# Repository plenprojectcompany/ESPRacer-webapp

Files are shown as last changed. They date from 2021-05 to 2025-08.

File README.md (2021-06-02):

ESPRacer for WebApp | PLEN Project Company Inc.
===============================================================================

## ESPRacer for WebApp

[ESPRacer for WebApp](https://plenprojectcompany.github.io/ESPRacer-webapp/)

## Copyright (c) 2021,
- [Isaki](https://github.com/IsakiMatsubara)
- [PLEN Project Company Inc.](https://plen.jp)

## License
This software is released under [the MIT License](http://opensource.org/licenses/mit-license.php).

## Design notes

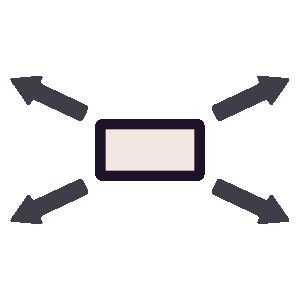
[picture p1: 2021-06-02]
image/Fullscreen-On.png

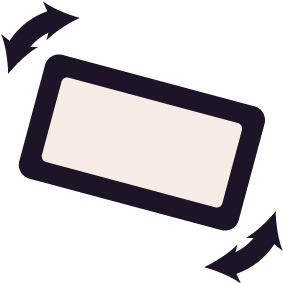
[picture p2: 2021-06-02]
image/Gyro-On.png

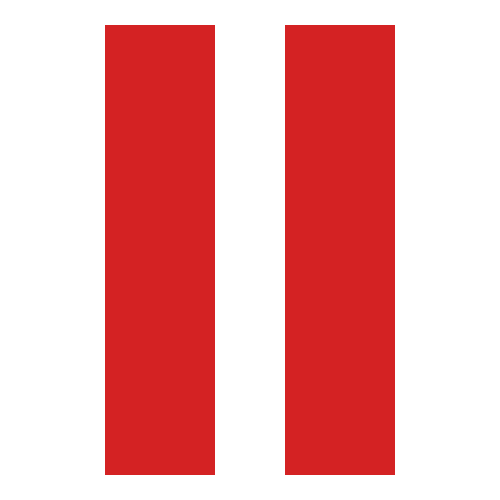
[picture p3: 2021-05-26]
image/CommandStop.png

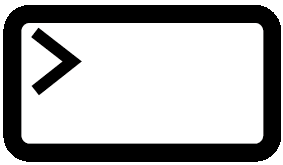
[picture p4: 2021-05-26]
image/Command.png

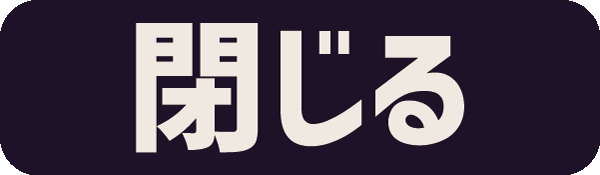
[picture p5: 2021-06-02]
image/Enter.png

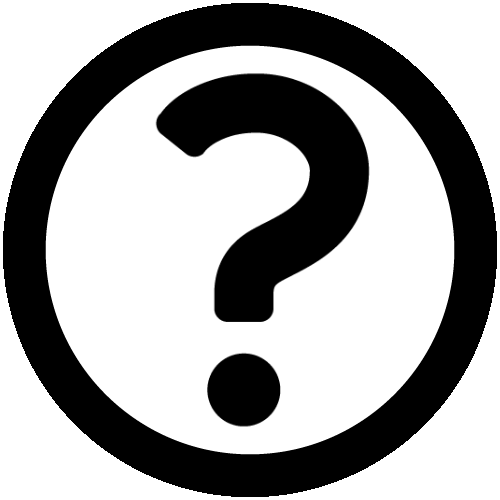
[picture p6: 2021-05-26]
image/Question.png

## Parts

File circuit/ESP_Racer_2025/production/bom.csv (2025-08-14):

Designator | Footprint | Quantity | Value | LCSC Part #
C1, C3, C4 | 0603 | 3 | 10u
C2, C5 | 0603 | 2 | 0.1u
D1 | 0603 | 1 | Status
IC1 | XCL103D503CRG | 1 | XCL102D333CR-G
J1 | Molex_PicoBlade_53047-0210_1x02_P1.25mm_Vertical | 1 | Conn_LED_1
J2 | Molex_PicoBlade_53047-0210_1x02_P1.25mm_Vertical | 1 | Conn_LED_2
J3 | Molex_PicoBlade_53047-0310_1x03_P1.25mm_Vertical | 1 | Conn_Servo
J4 | Serial | 1 | Conn_USB
Q3 | SOT23 | 1 | IRLML6402
R1, R4, R7 | 0603 | 3 | 10k
R2, R3 | 0603 | 2 | 300
R5 | 0603 | 1 | 1k
R6 | 0603 | 1 | 20k
U1 | SON50P300X200X80-13N | 1 | DRV8835DSST
U2 | FCI_SFV12R-2STE1LF | 1 | SFV12R-2STE1LF | SFV12R-2STE1LF
U3 | ESP32-C3-WROOM-02 | 1 | ESP32-C3-WROOM-02

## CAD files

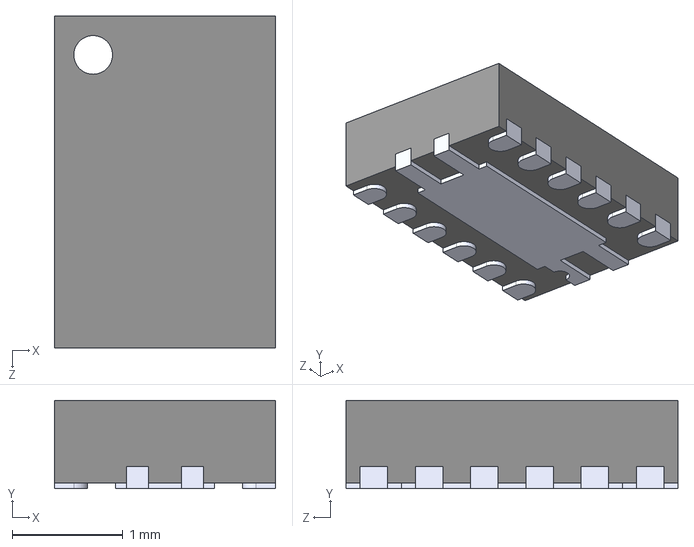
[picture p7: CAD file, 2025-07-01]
circuit/Footprint/DRV8835DSST/DRV8835DSST.step
2.00 x 0.8 x 3.00 mm

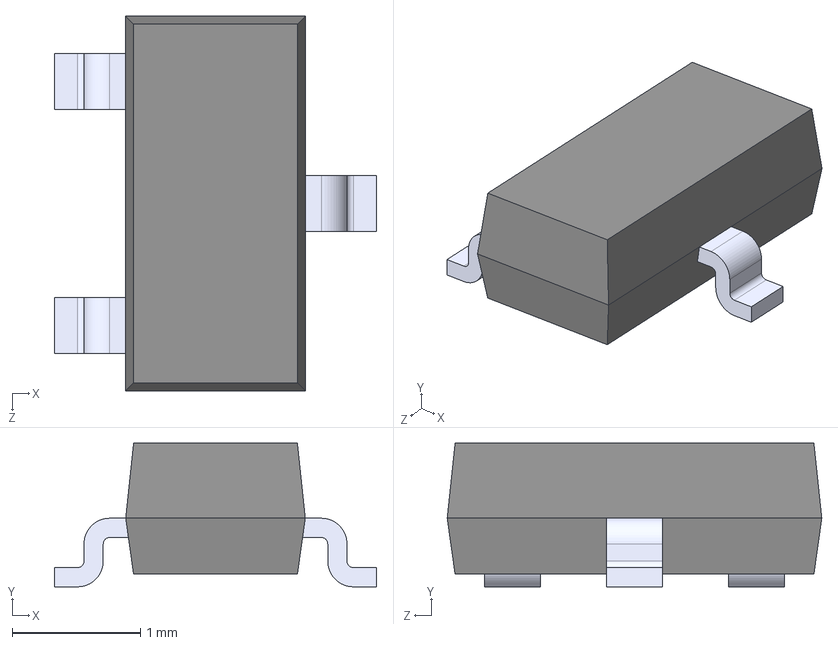
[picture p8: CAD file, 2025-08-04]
circuit/Footprint/IRLML6402/IRLML6402.step
2.51 x 1.12 x 2.92 mm

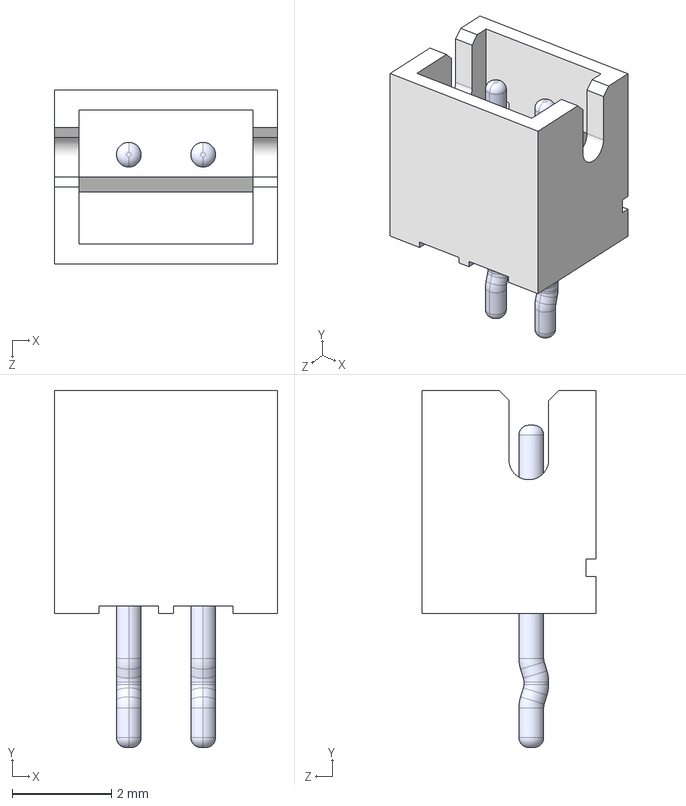
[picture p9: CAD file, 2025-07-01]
circuit/Footprint/JST_ZH_B2B-ZR_1x02_P1.50mm_Vertical/JST_ZH_B2B-ZR_1x02_P1.50mm_Vertical.STEP
4.50 x 7.20 x 3.50 mm
BxB-ZR_2
pin_Bent x 2

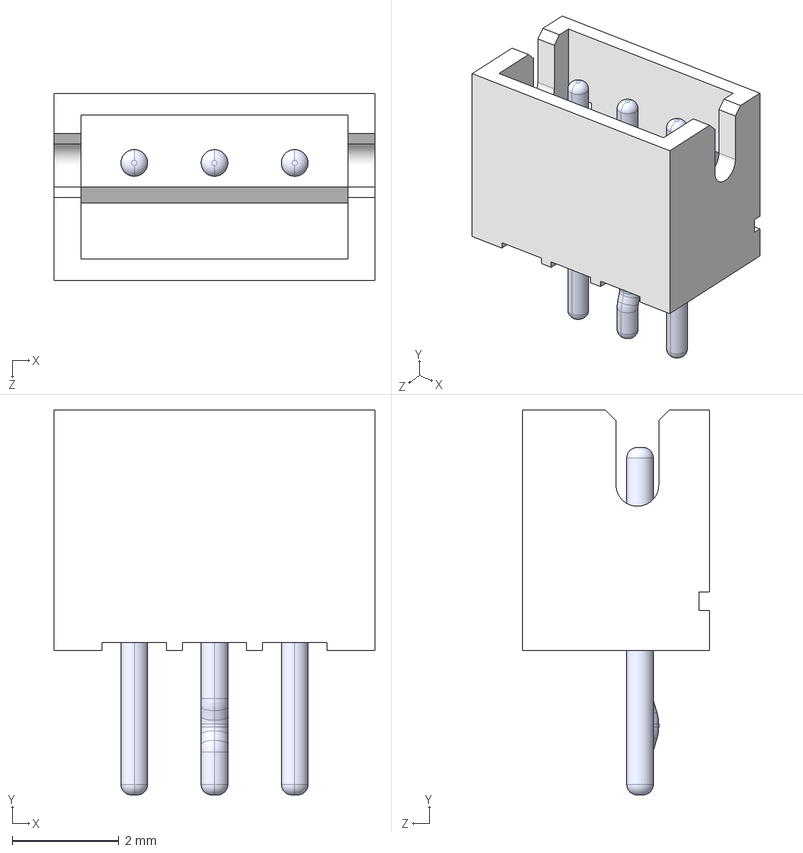
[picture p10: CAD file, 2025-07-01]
circuit/Footprint/JST_ZH_B3B-ZR_1x03_P1.50mm_Vertical/JST_ZH_B3B-ZR_1x03_P1.50mm_Vertical.STEP
6.00 x 7.20 x 3.50 mm
BxB-ZR_3
pin_straight x 2
pin_Bent

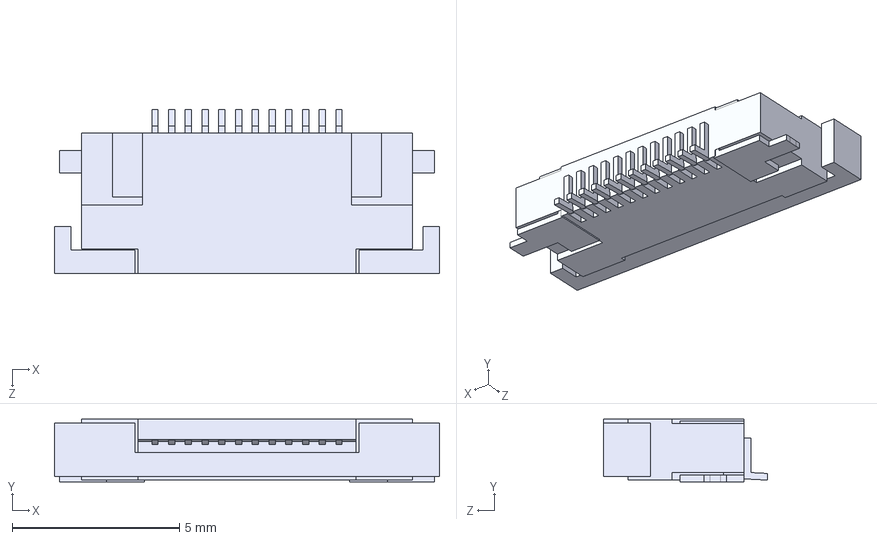
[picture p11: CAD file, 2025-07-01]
circuit/Footprint/SFV12R-2STE1LF/SFV12R-2STE1LF.step
11.5 x 1.87 x 4.90 mm

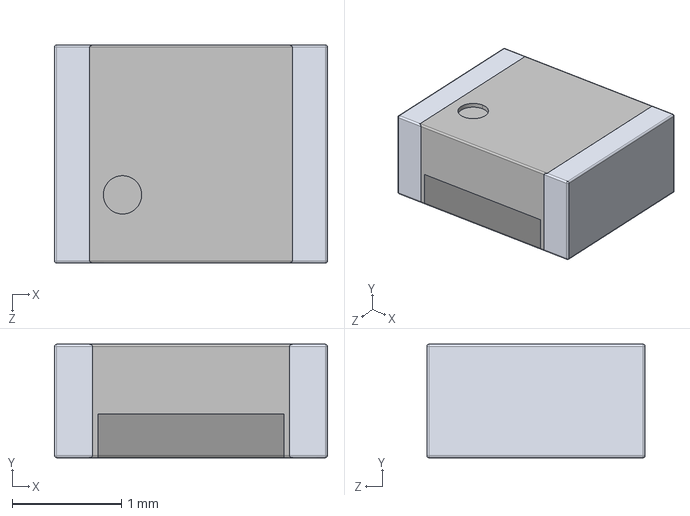
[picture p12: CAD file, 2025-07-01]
circuit/Footprint/XCL102D333CR-G/XCL102D333CR-G.stp
2.50 x 1.04 x 2.00 mm

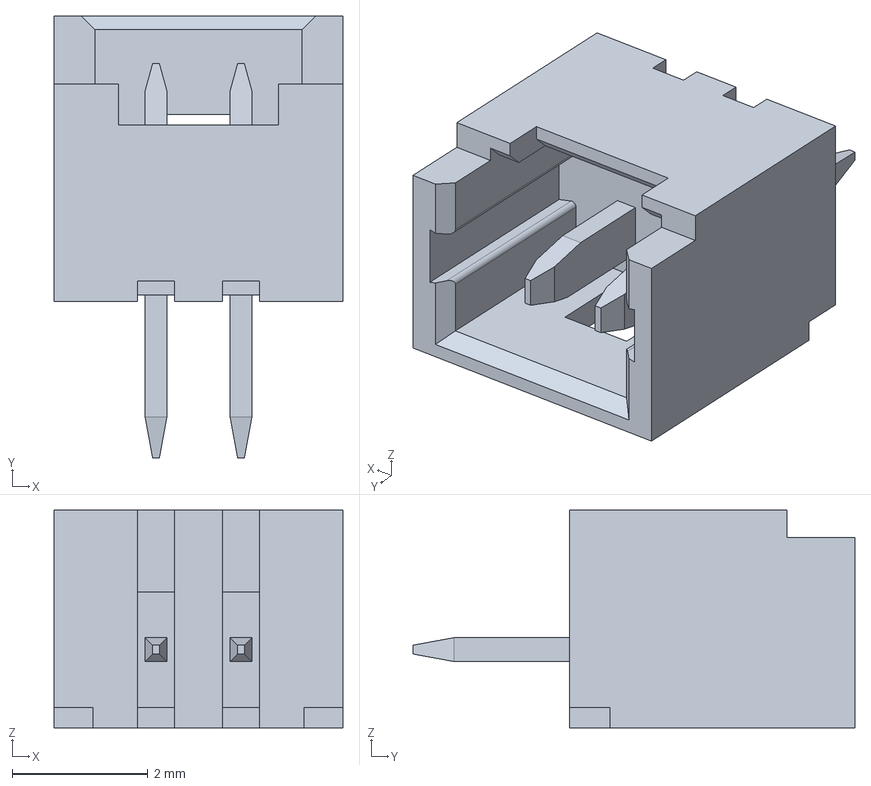
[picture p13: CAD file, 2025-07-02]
circuit/Footprint/53047-0210/53047-0210.step
4.25 x 6.50 x 3.20 mm

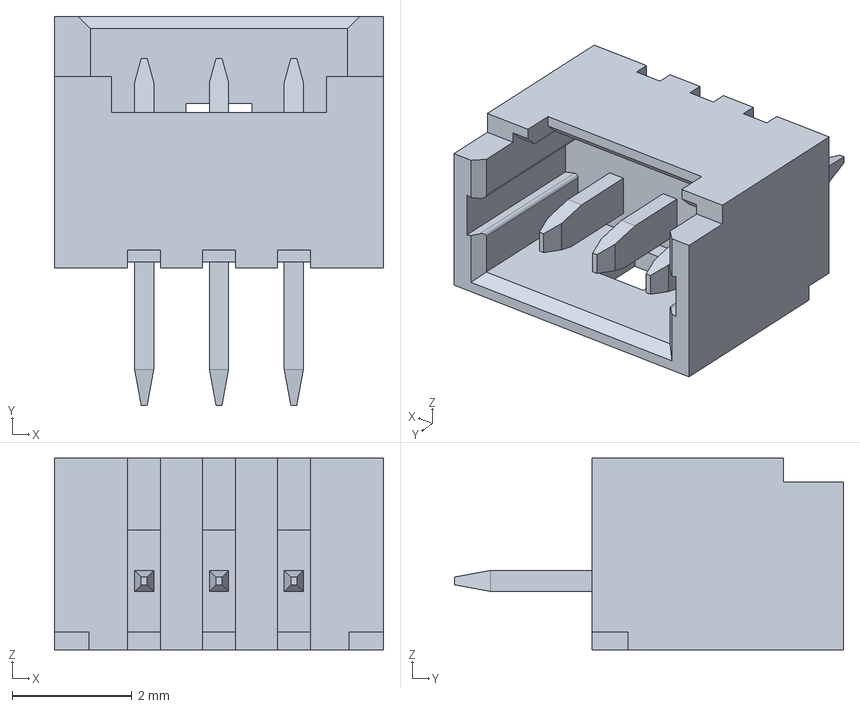
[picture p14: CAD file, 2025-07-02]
circuit/Footprint/53047-0310/53047-0310.step
5.50 x 6.50 x 3.20 mm

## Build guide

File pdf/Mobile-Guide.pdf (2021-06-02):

P.

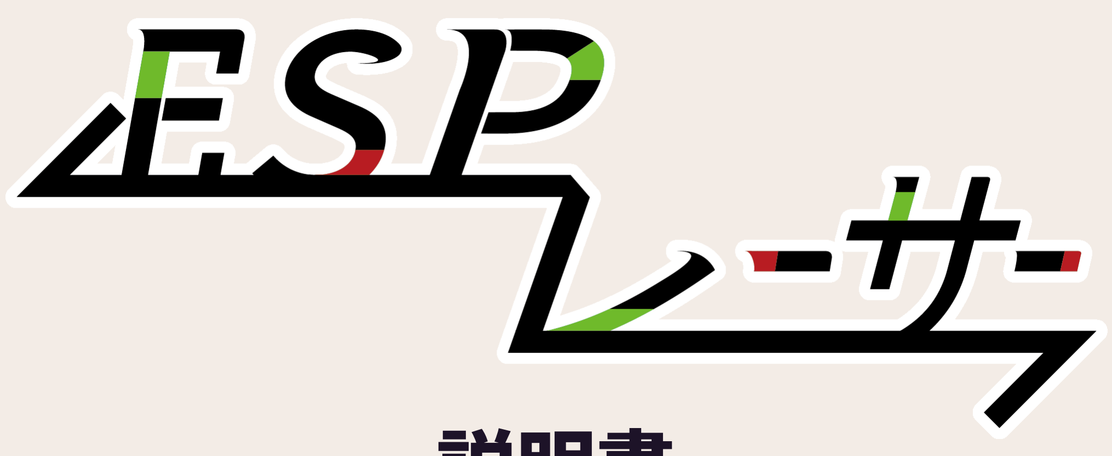
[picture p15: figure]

# 説明書

# ESPレーサー for WebApp

0

# ESPレーサーforWebApp

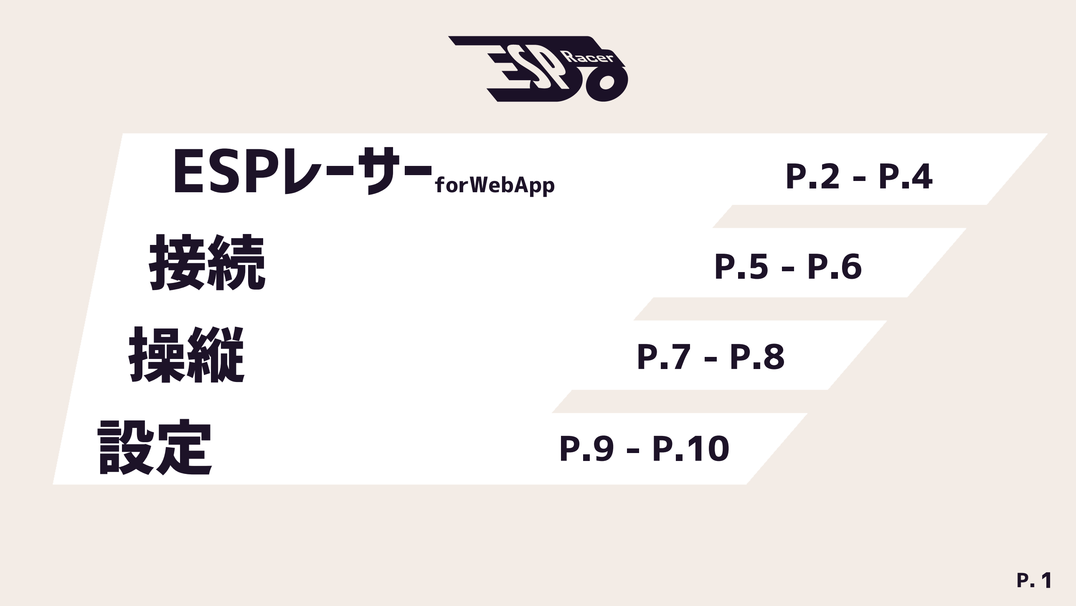
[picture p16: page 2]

P. 1

接続
操縦
設定

P.2 - P.4

P.5 - P.6

P.7 - P.8

P.9 - P.10

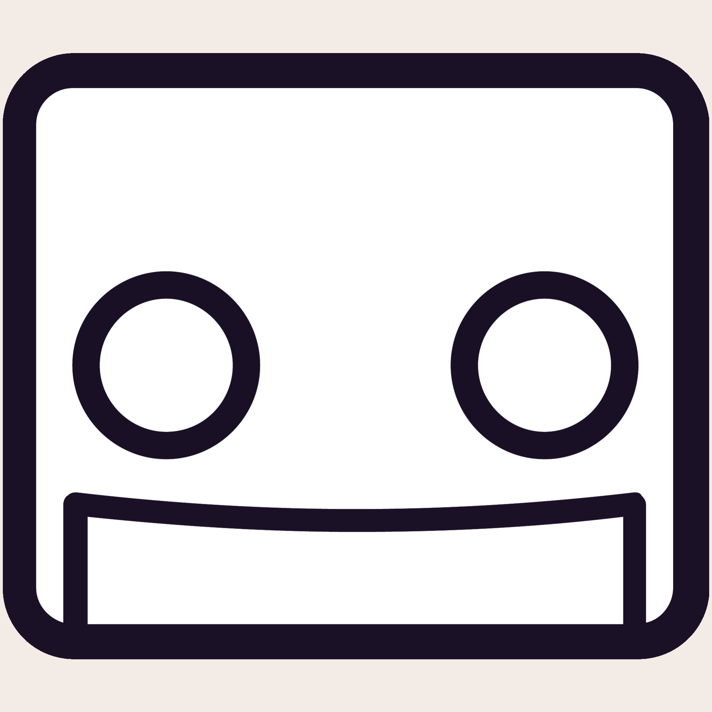
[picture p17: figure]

# ESPレーサー for WebApp

概要

2

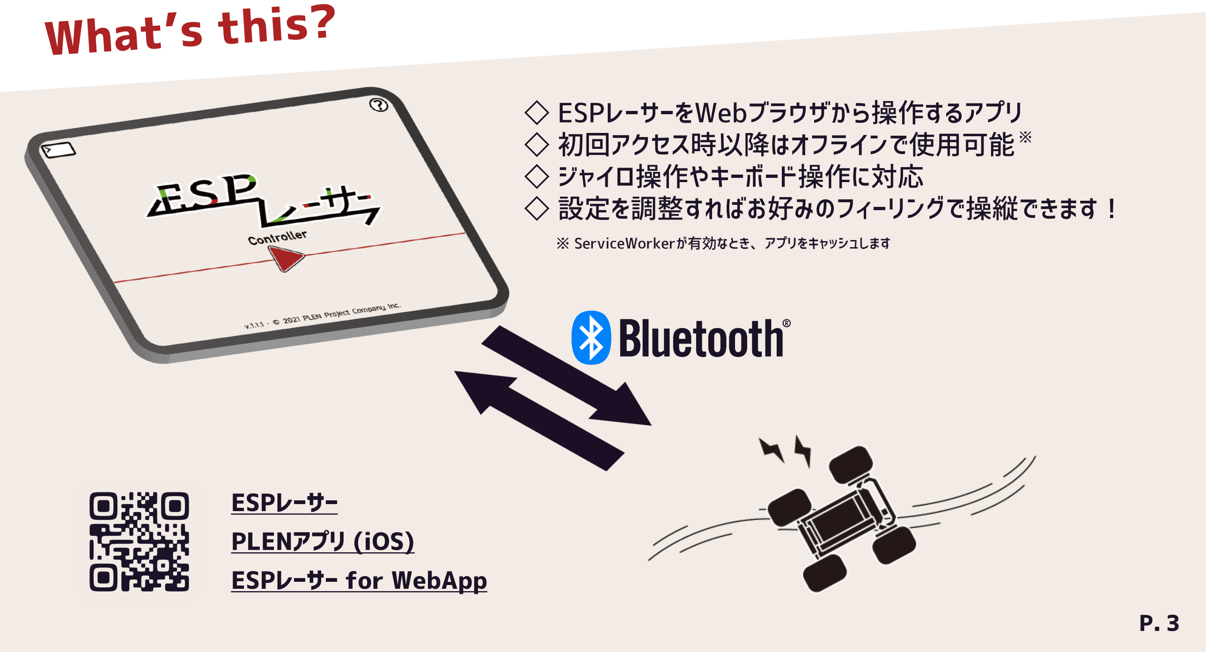
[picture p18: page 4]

P. 3

ESPレーサー for WebApp (https://plenprojectcompany.github.io/ESPRacer-webapp/index.html)

ESPレーサー (https://plen.jp/espracer/)
PLENアプリ (iOS) (https://apps.apple.com/jp/app/plen/id1561905612)

◇ ESPレーサーをWebブラウザから操作するアプリ
◇ 初回アクセス時以降はオフラインで使用可能
◇ ジャイロ操作やキーボード操作に対応
◇ 設定を調整すればお好みのフィーリングで操縦できます！

※ ServiceWorkerが有効なとき、アプリをキャッシュします

※

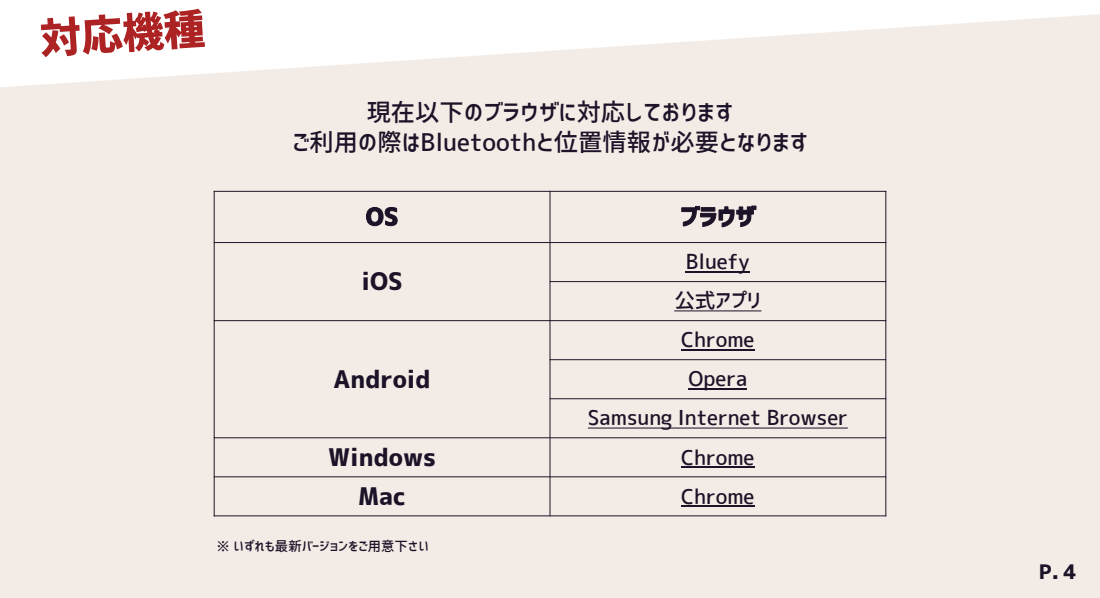
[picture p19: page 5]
公式アプリ; Android; Chrome; Opera; 現在以下のブラウザに対応しております ご利用の際はBluetoothと位置情報が必要となります; ※ いずれも最新バージョンをご用意下さい

OS | ブラウザ

iOS | Bluefy (https://apps.apple.com/us/app/bluefy-web-ble-browser/id1492822055)

Samsung Internet Browser (https://play.google.com/store/apps/details?id=com.sec.android.app.sbrowser)

Windows | Chrome (https://www.google.com/intl/ja_jp/chrome/)
Mac | Chrome (https://www.google.com/intl/ja_jp/chrome/)

接続

## 接続にはBluetoothが必要です

5

注意

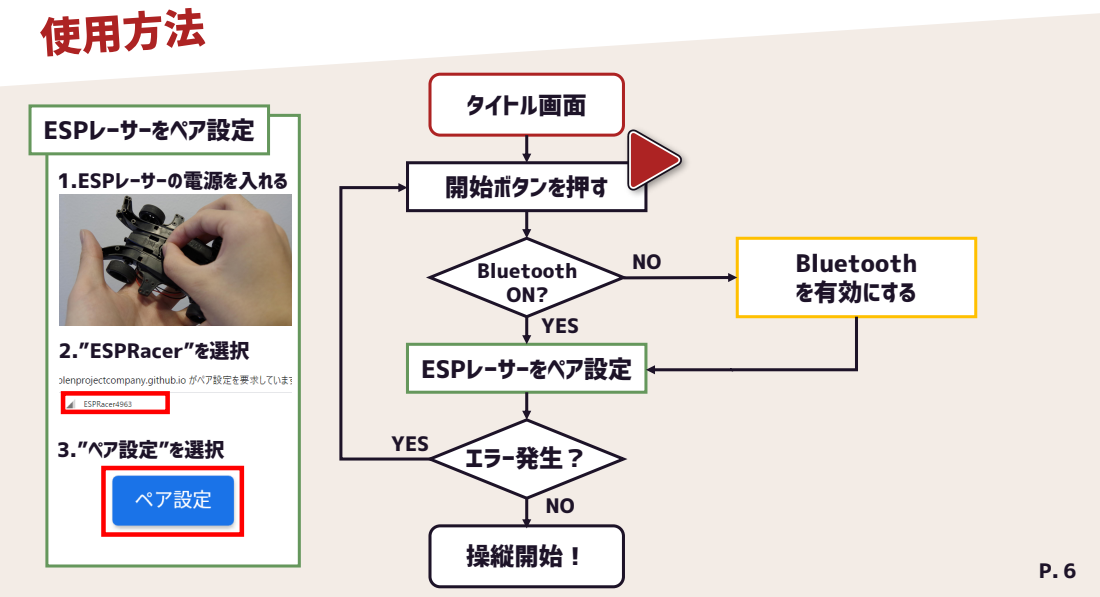
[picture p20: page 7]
タイトル画面; Bluetooth ON?; ESPレーサーをペア設定; 開始ボタンを押す; Bluetooth を有効にする; エラー発生？; 操縦開始！; YES; 1.ESPレーサーの電源を入れる; 2.”ESPRacer”を選択; 3.”ペア設定”を選択

操縦

## スマートフォンではジャイロ操作、PCではキーボード操作が可能です

7

注意

## LED

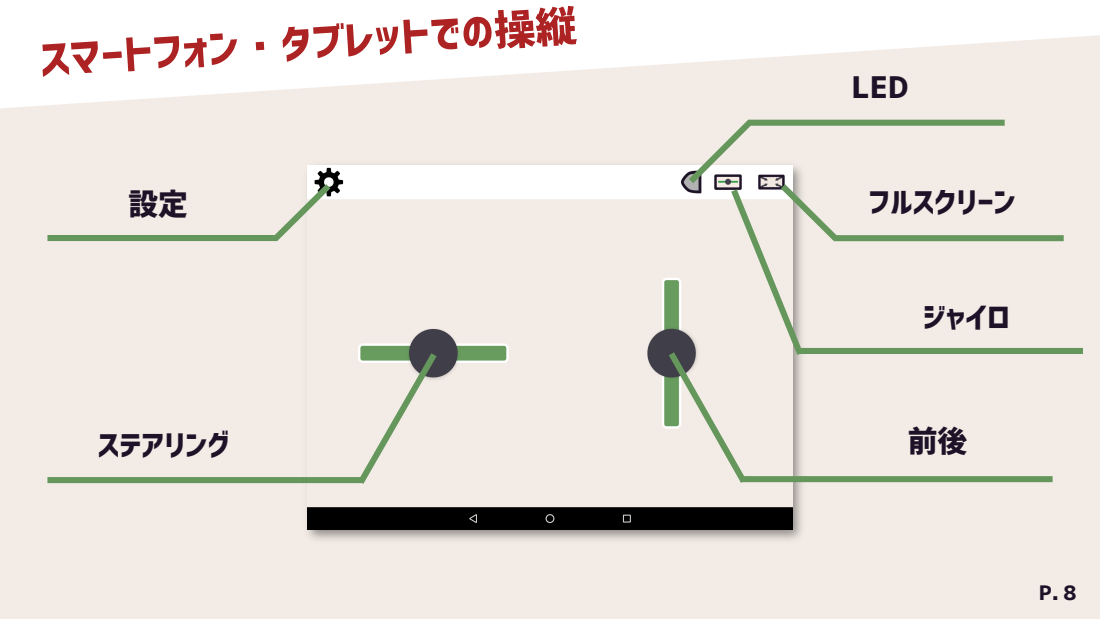
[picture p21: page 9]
ステアリング; フルスクリーン; ジャイロ

設定

## 変更した設定内容はブラウザに保存されます

9

注意

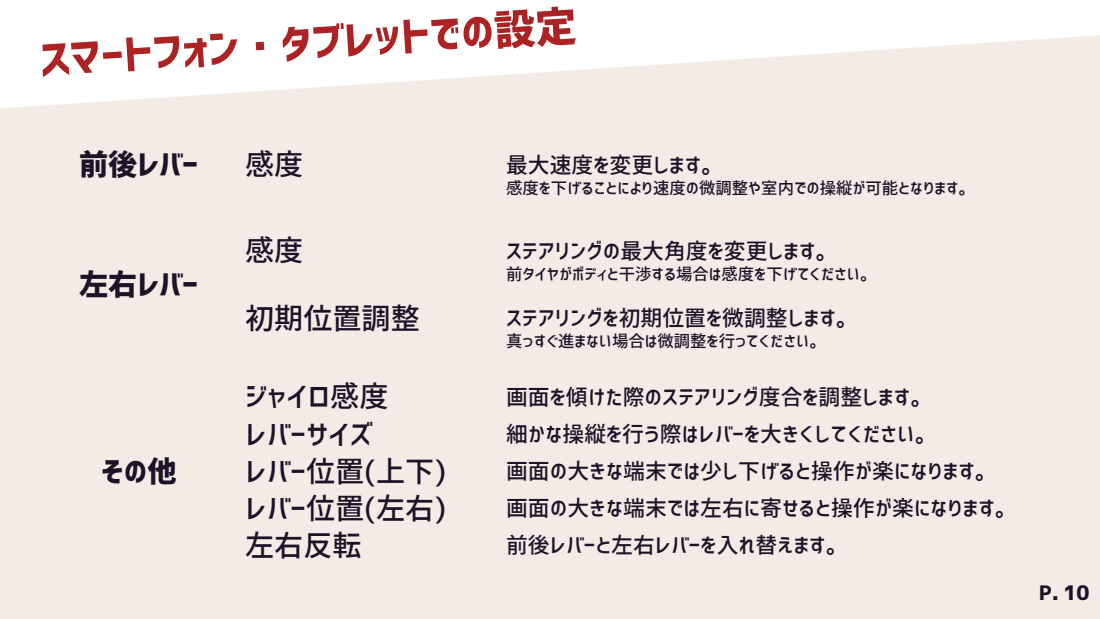
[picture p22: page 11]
前後レバー; 最大速度を変更します。; 感度を下げることにより速度の微調整や室内での操縦が可能となります。; 左右レバー; ステアリングの最大角度を変更します。; 前タイヤがボディと干渉する場合は感度を下げてください。; 初期位置調整; ステアリングを初期位置を微調整します。; 真っすぐ進まない場合は微調整を行ってください。; その他; ジャイロ感度; 画面を傾けた際のステアリング度合を調整します。; レバーサイズ; 細かな操縦を行う際はレバーを大きくしてください。; レバー位置(上下); 画面の大きな端末では少し下げると操作が楽になります。; レバー位置(左右); 画面の大きな端末では左右に寄せると操作が楽になります。; 左右反転; 前後レバーと左右レバーを入れ替えます。

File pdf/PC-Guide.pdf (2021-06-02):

P.


# 説明書

# ESPレーサー for WebApp

0

# ESPレーサーforWebApp

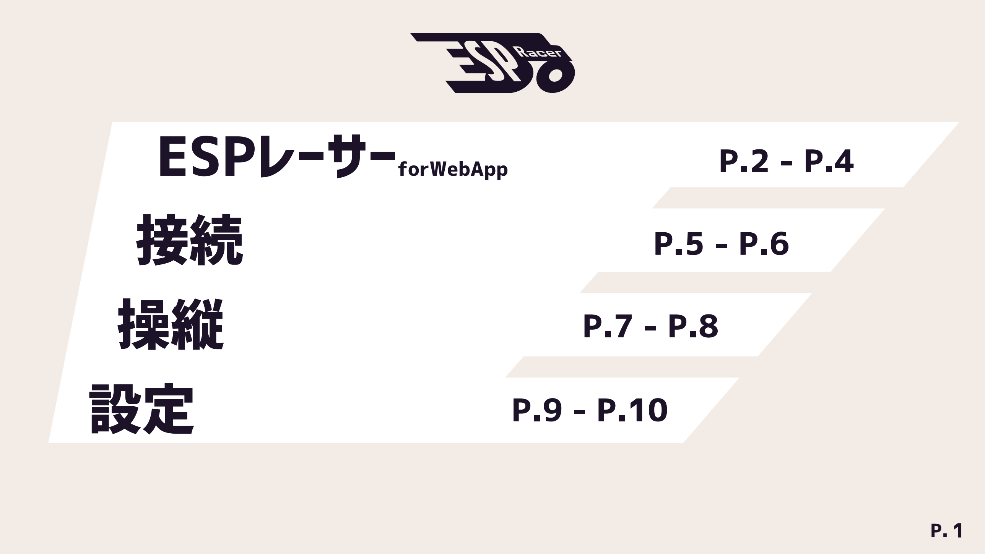
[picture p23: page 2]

P. 1

接続
操縦
設定

P.2 - P.4

P.5 - P.6

P.7 - P.8

P.9 - P.10


# ESPレーサー for WebApp

概要

2


P. 3

ESPレーサー for WebApp (https://plenprojectcompany.github.io/ESPRacer-webapp/index.html)

ESPレーサー (https://plen.jp/espracer/)
PLENアプリ (iOS) (https://apps.apple.com/jp/app/plen/id1561905612)

◇ ESPレーサーをWebブラウザから操作するアプリ
◇ 初回アクセス時以降はオフラインで使用可能
◇ ジャイロ操作やキーボード操作に対応
◇ 設定を調整すればお好みのフィーリングで操縦できます！

※ ServiceWorkerが有効なとき、アプリをキャッシュします

※

公式アプリ; Android; Chrome; Opera; 現在以下のブラウザに対応しております ご利用の際はBluetoothと位置情報が必要となります; ※ いずれも最新バージョンをご用意下さい

OS | ブラウザ

iOS | Bluefy (https://apps.apple.com/us/app/bluefy-web-ble-browser/id1492822055)

Samsung Internet Browser (https://play.google.com/store/apps/details?id=com.sec.android.app.sbrowser)

Windows | Chrome (https://www.google.com/intl/ja_jp/chrome/)
Mac | Chrome (https://www.google.com/intl/ja_jp/chrome/)

接続

## 接続にはBluetoothが必要です

5

注意

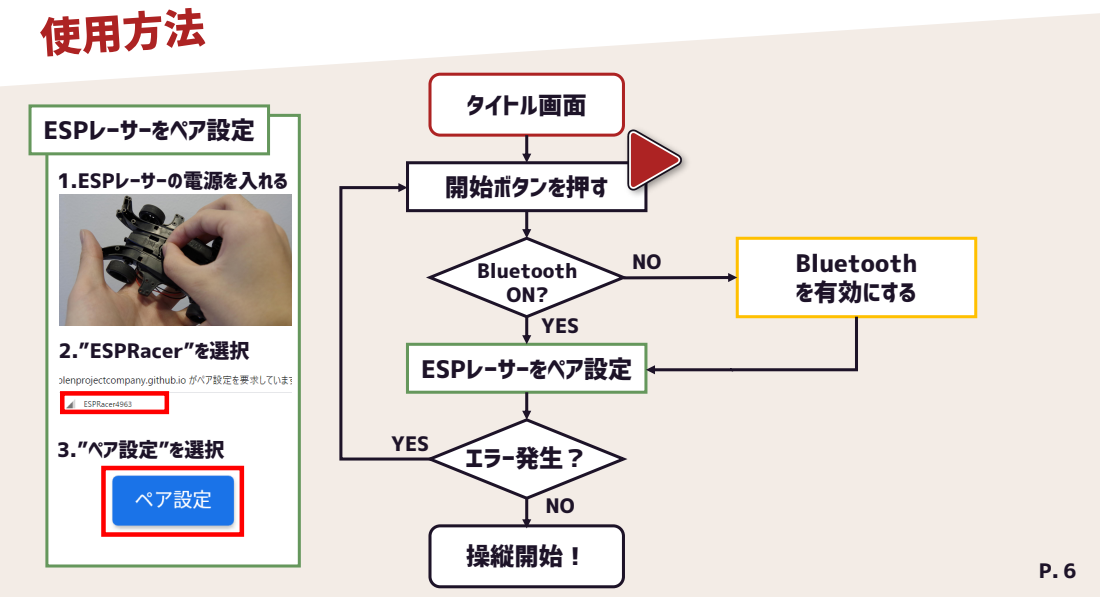
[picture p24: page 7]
タイトル画面; Bluetooth ON?; ESPレーサーをペア設定; 開始ボタンを押す; Bluetooth を有効にする; エラー発生？; 操縦開始！; YES; 1.ESPレーサーの電源を入れる; 2.”ESPRacer”を選択; 3.”ペア設定”を選択

操縦

## スマートフォンではジャイロ操作、PCではキーボード操作が可能です

7

注意

## LED

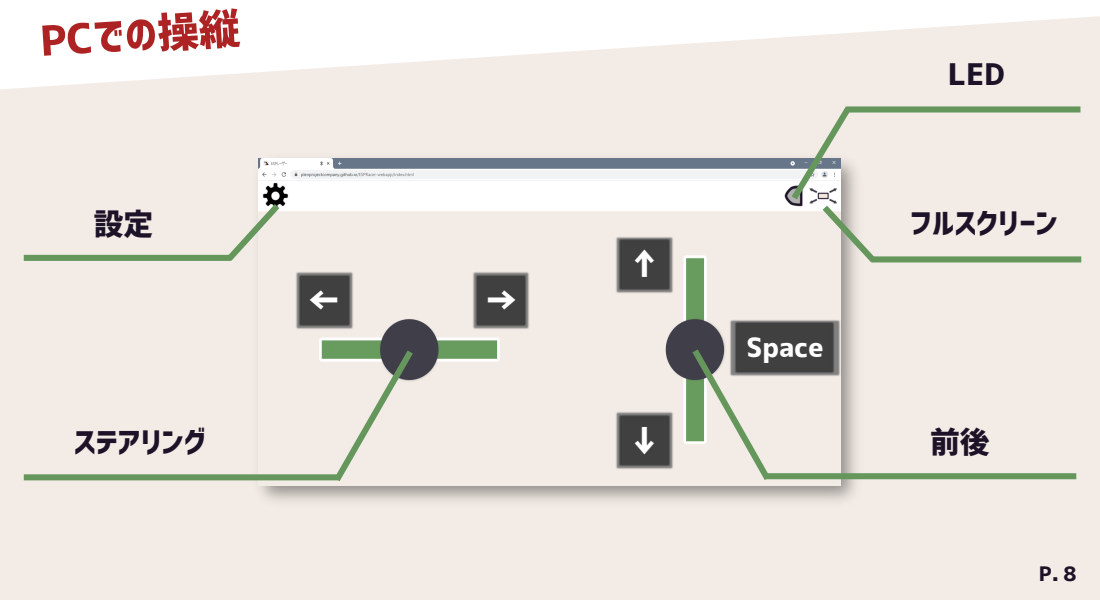
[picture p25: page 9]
ステアリング; フルスクリーン; Space

設定

## 変更した設定内容はブラウザに保存されます

9

注意

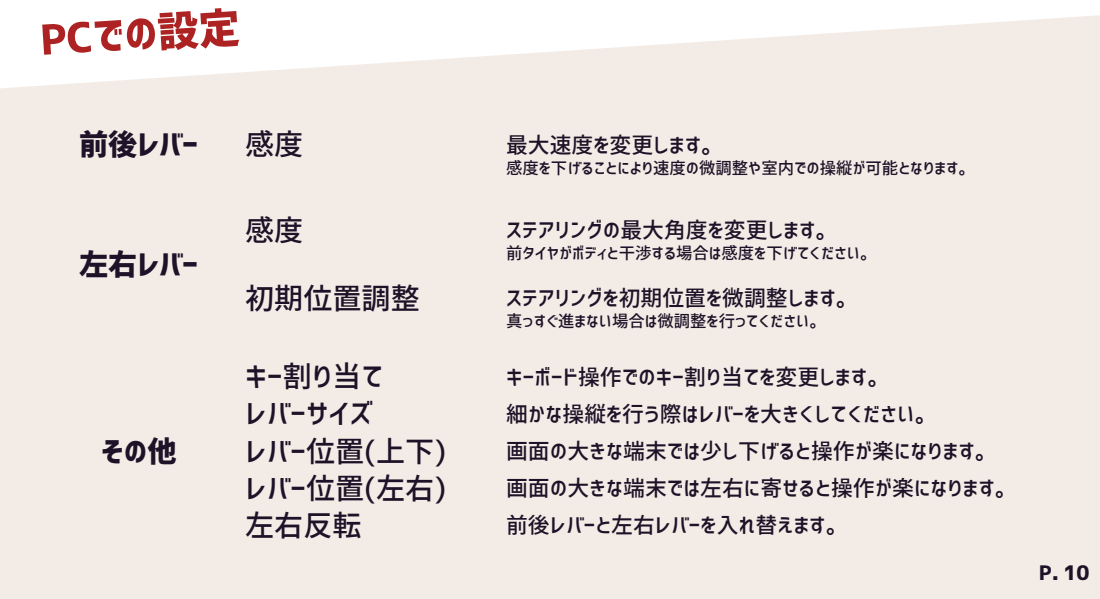
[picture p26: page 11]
前後レバー; 最大速度を変更します。; 感度を下げることにより速度の微調整や室内での操縦が可能となります。; 左右レバー; ステアリングの最大角度を変更します。; 前タイヤがボディと干渉する場合は感度を下げてください。; 初期位置調整; ステアリングを初期位置を微調整します。; 真っすぐ進まない場合は微調整を行ってください。; その他; キー割り当て; キーボード操作でのキー割り当てを変更します。; レバーサイズ; 細かな操縦を行う際はレバーを大きくしてください。; レバー位置(上下); 画面の大きな端末では少し下げると操作が楽になります。; レバー位置(左右); 画面の大きな端末では左右に寄せると操作が楽になります。; 左右反転; 前後レバーと左右レバーを入れ替えます。

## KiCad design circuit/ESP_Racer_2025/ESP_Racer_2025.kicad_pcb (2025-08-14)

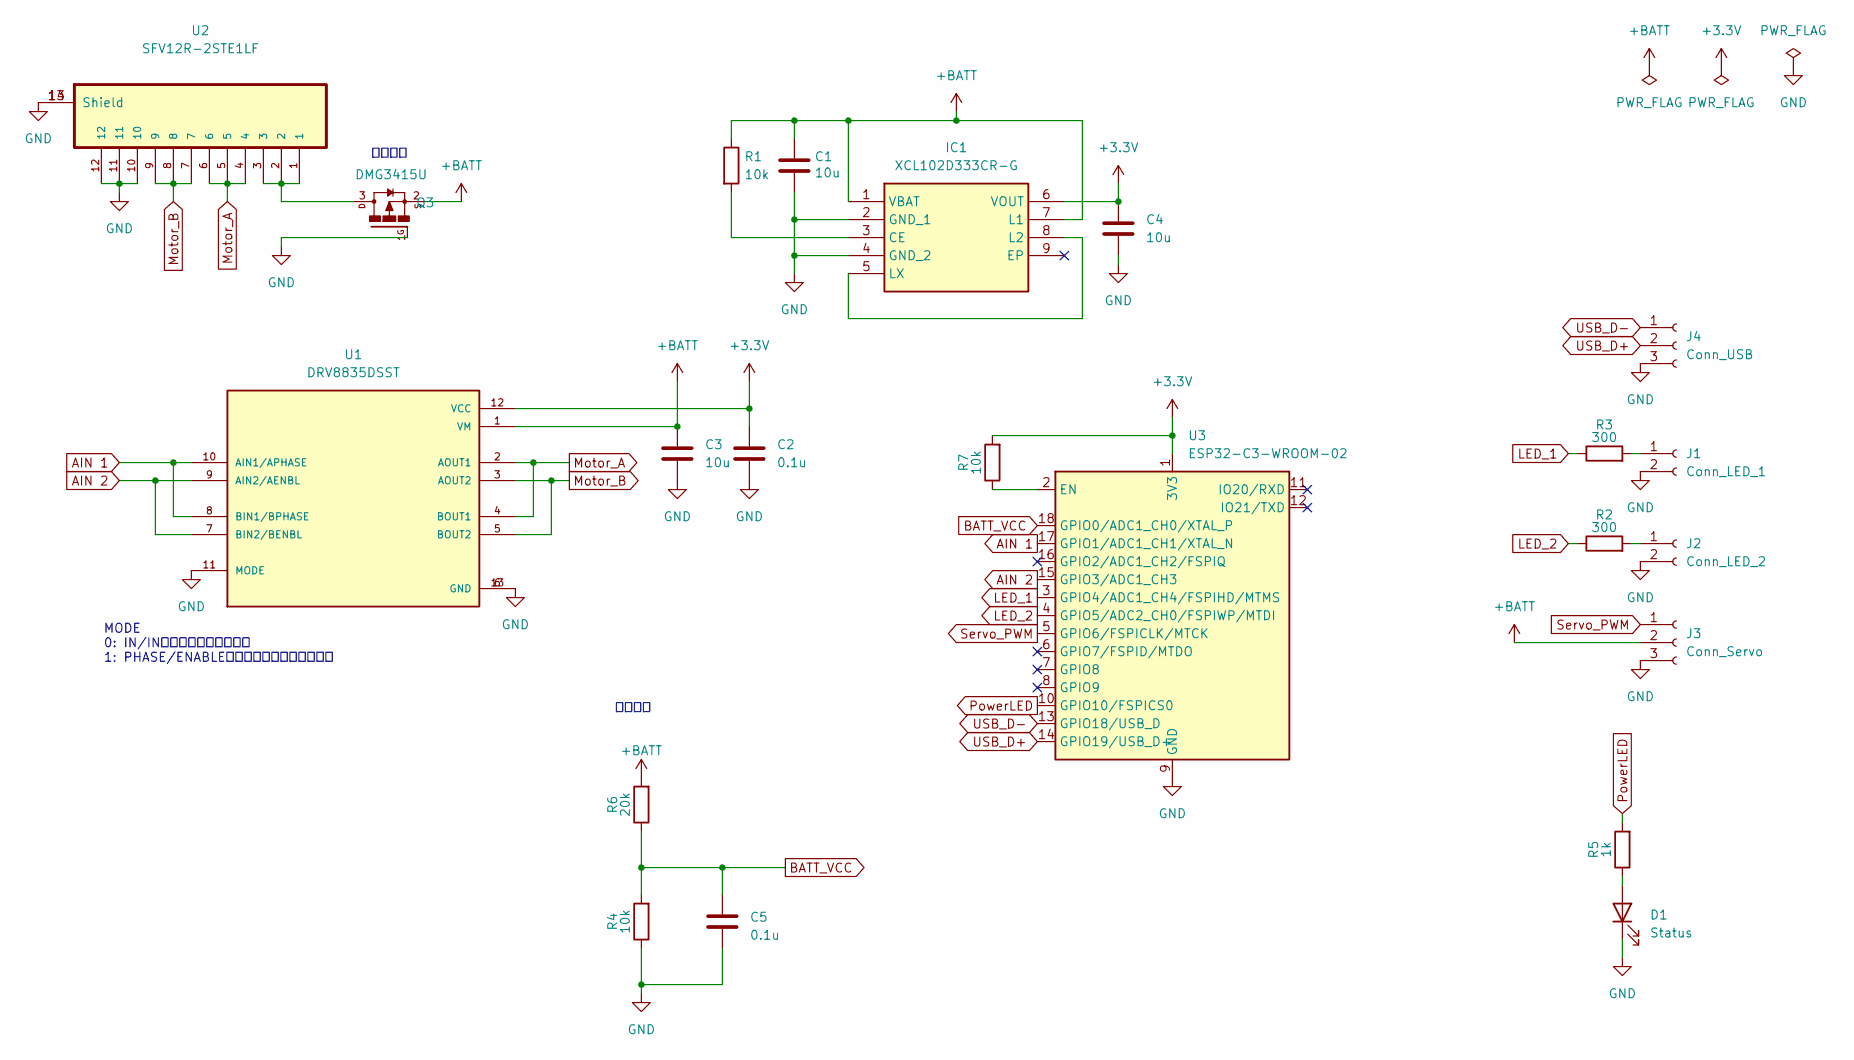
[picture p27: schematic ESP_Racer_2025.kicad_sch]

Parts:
C1, C3, C4: 10u; C_0603_1608Metric_Pad1.08x0.95mm_HandSolder
C2, C5: 0.1u; C_0603_1608Metric_Pad1.08x0.95mm_HandSolder
D1: Status; LED_0603_1608Metric_Pad1.05x0.95mm_HandSolder
IC1: XCL102D333CR-G; XCL103D503CRG; Manufacturer_Part_Number XCL102D333CR-G
J1: Conn_LED_1; Molex_PicoBlade_53047-0210_1x02_P1.25mm_Vertical
J2: Conn_LED_2; Molex_PicoBlade_53047-0210_1x02_P1.25mm_Vertical
J3: Conn_Servo; Molex_PicoBlade_53047-0310_1x03_P1.25mm_Vertical
J4: Conn_USB; Serial
Q3: DMG3415U; SOT23
R1, R4, R7: 10k; R_0603_1608Metric_Pad0.98x0.95mm_HandSolder
R2, R3: 300; R_0603_1608Metric_Pad0.98x0.95mm_HandSolder
R5: 1k; R_0603_1608Metric_Pad0.98x0.95mm_HandSolder
R6: 20k; R_0603_1608Metric_Pad0.98x0.95mm_HandSolder
U1: DRV8835DSST; SON50P300X200X80-13N; PARTREV H
U2: SFV12R-2STE1LF; FCI_SFV12R-2STE1LF; MPN SFV12R-2STE1LF
U3: ESP32-C3-WROOM-02

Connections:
+3.3V: C2.1, C4.1, IC1.6 (VOUT), R7.2, U1.12 (VCC), U3.1 (3V3)
+BATT: C1.1, C3.1, IC1.1 (VBAT), IC1.7 (L1), J3.2, Q3.2, R1.1, R6.2, U1.1 (VM)
AIN 1: U1.8 (BIN1/BPHASE), U1.10 (AIN1/APHASE), U3.17 (GPIO1/ADC1_CH1/XTAL_N)
AIN 2: U1.7 (BIN2/BENBL), U1.9 (AIN2/AENBL), U3.15 (GPIO3/ADC1_CH3)
BATT_VCC: C5.1, R4.2, R6.1, U3.18 (GPIO0/ADC1_CH0/XTAL_P)
GND: C1.2, C2.2, C3.2, C4.2, C5.2, D1.1 (K), IC1.2 (GND_1), IC1.4 (GND_2), J1.2, J2.2, J3.3, J4.3, Q3.1, R4.1, U1.6 (GND), U1.11 (MODE), U1.13 (GND), U2.10, U2.11, U2.12, U2.13 (Shield), U2.14 (Shield), U3.9 (GND), U3.19 (GND)
LED_1: R3.1, U3.3 (GPIO4/ADC1_CH4/FSPIHD/MTMS)
LED_2: R2.1, U3.4 (GPIO5/ADC2_CH0/FSPIWP/MTDI)
Motor_A: U1.2 (AOUT1), U1.4 (BOUT1), U2.4, U2.5, U2.6
Motor_B: U1.3 (AOUT2), U1.5 (BOUT2), U2.7, U2.8, U2.9
unnamed: D1.2 (A), R5.1
unnamed: IC1.3 (CE), R1.2
unnamed: IC1.5 (LX), IC1.8 (L2)
unnamed: J1.1, R3.2
unnamed: J2.1, R2.2
unnamed: Q3.3, U2.1, U2.2, U2.3
unnamed: R7.1, U3.2 (EN)
PowerLED: R5.2, U3.10 (GPIO10/FSPICS0)
Servo_PWM: J3.1, U3.5 (GPIO6/FSPICLK/MTCK)
USB_D+: J4.2, U3.14 (GPIO19/USB_D+)
USB_D-: J4.1, U3.13 (GPIO18/USB_D)

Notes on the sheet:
MODE 0: IN/INモード（慣性で停止） 1: PHASE/ENABLEモード（ブレーキで停止）
電圧監視
逆接防止

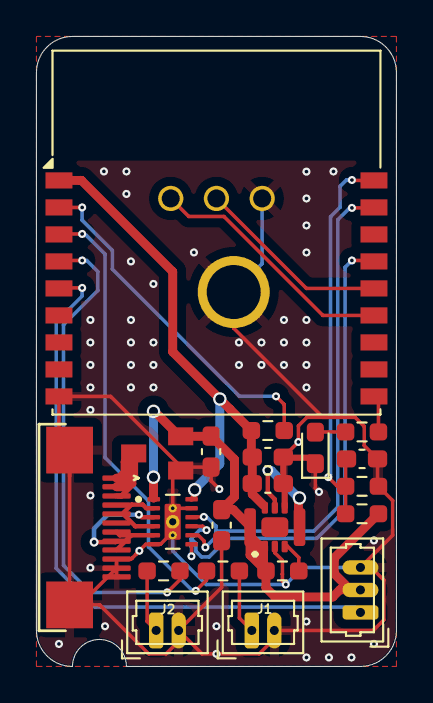
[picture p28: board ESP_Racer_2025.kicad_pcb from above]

Board: 2 copper layers, 20.0 x 35.0 mm, 22 parts (1 on the bottom side), 21 nets.

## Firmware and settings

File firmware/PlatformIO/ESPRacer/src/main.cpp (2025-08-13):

#include <Arduino.h>
#include <math.h>
#include <Wire.h>

#include <Preferences.h>

// Bluetooth Low Energy
#include "BLE/BLE.h"

#define ARRAY_LENGTH(array) (sizeof(array) / sizeof(array[0]))

#define debugMode true

/*========== Version ==========*/
#define FIRMWARE_VER "F1.02"
#define HARDWARE_VER "H1.01"

/*========== Class ==========*/
Preferences pref;

/*========== Hardware Functions ==========*/
#define MOTOR_CH 0b10 // モーターCh1
#define SERVO_CH 0b0001 // サーボ Ch0
#define PORT_CH 0b0011 // LEDポート Ch0, Ch1

/*========== I/O (ESP32-C3) ==========*/
#define STATUS_LED_PIN  10
#define SERVO_PIN  6
#define MOTOR_A_PIN 1
#define MOTOR_B_PIN 3
#define PORT_0_PIN  4
#define PORT_1_PIN  5 
#define BATT_VOL_PIN  0

#define CHANNEL_STATUS_LED_PIN 0
#define CHANNEL_SERVO_PIN 1
#define CHANNEL_MOTOR_A_PIN 2
#define CHANNEL_MOTOR_B_PIN 3

#define SERVO_FREQUENCY 50 // 50 [Hz] = 20 [ms] / 1周期
#define SERVO_RESOLUTION 12 // 12bit=4096
#define SERVO_TIME_MIN 102 // 0.5 [ms] / 20 [ms] * 4096 = 102.4
#define SERVO_TIME_MAX 492 // 2.4 [ms] / 20 [ms] * 4096 = 491.52  491.52-102.4=389.12 > 256 (OK)

/*========== BLE UUID ==========*/
#define ADVERTISING_UUID    "389CAAF0-843F-4D3B-959D-C954CCE14655"
#define SERVICE_UUID        "389CAAF0-843F-4D3B-959D-C954CCE14655"
#define GET_BATTERY_VOLTAGE "389CAAF1-843F-4D3B-959D-C954CCE14655"
#define SET_MOTOR_PWM       "389CAAF2-843F-4D3B-959D-C954CCE14655"
#define SET_PORT_OUT        "389CAAF3-843F-4D3B-959D-C954CCE14655"
#define SET_SERVO_POSITION  "389CAAF4-843F-4D3B-959D-C954CCE14655"
#define BURST_COMMAND       "389CAAF5-843F-4D3B-959D-C954CCE14655"
#define GET_FUNCTIONS       "389CAAFF-843F-4D3B-959D-C954CCE14655"

/*========== BLE CharaCharacteristic ==========*/
BLECharacteristic *GET_BATTERY_VOLTAGE_CHARA;
BLECharacteristic *SET_MOTOR_PWM_CHARA;
BLECharacteristic *SET_PORT_OUT_CHARA;
BLECharacteristic *SET_SERVO_POSITION_CHARA;
BLECharacteristic *BURST_COMMAND_CHARA;
BLECharacteristic *GET_FUNCTIONS_CHARA;

BLE RacerBLE = BLE("ESPRacer", true);

/*========== Parameters ==========*/
const int deviceIdLen = 10;
const int sendFreqency = 50; // [ms]
const bool motorInv = false;
const bool servoInv = false;

/*========== Private Variable ==========*/
bool deviceConnectedFlag = false;
int lastSendTime = 0;
int ledBlinkTime = 0;
// unsigned char motor_power = 127;
// unsigned char servo_power = 127;
// bool port0_led = false;
// bool port1_led = false;

void HardwareReset();

void SetupRacer()
{
  pinMode(STATUS_LED_PIN, OUTPUT);
  pinMode(SERVO_PIN,OUTPUT);
  pinMode(MOTOR_A_PIN, OUTPUT);
  pinMode(MOTOR_B_PIN, OUTPUT);
  pinMode(PORT_0_PIN, OUTPUT);
  pinMode(PORT_1_PIN, OUTPUT);
  pinMode(BATT_VOL_PIN, INPUT);

  // pwmの設定 channel,周波数,解像度
  ledcSetup(CHANNEL_STATUS_LED_PIN, 1000, 8);
  ledcSetup(CHANNEL_SERVO_PIN, SERVO_FREQUENCY, SERVO_RESOLUTION);
  ledcSetup(CHANNEL_MOTOR_A_PIN, 1000, 7);
  ledcSetup(CHANNEL_MOTOR_B_PIN, 1000, 7);
  // ピンをチャンネルに接続
  ledcAttachPin(STATUS_LED_PIN, CHANNEL_STATUS_LED_PIN);
  ledcAttachPin(SERVO_PIN, CHANNEL_SERVO_PIN);
  ledcAttachPin(MOTOR_A_PIN, CHANNEL_MOTOR_A_PIN);
  ledcAttachPin(MOTOR_B_PIN, CHANNEL_MOTOR_B_PIN);

  ledcWrite(CHANNEL_STATUS_LED_PIN, 255);

  HardwareReset();
}

String GenerateID(int len)
{
  char id[len];

  for (int i = 0; i < len; i++)
  {
    int random = esp_random() % 36; // 0~35の乱数 (数字10個、アルファベット26個)

    if (random < 10)
    {
      id[i] = random + 48; // 数字
    }
    else
    {
      id[i] = random + 55; // アルファベット
    }
  }

  return String(id);
}

void onMotorPWMReceived(const std::string& value);
void onPortOUTReceived(const std::string& value);
void onServoPWMReceived(const std::string& value);
void onBurstCommandReceived(const std::string& value);

void SetupBLE()
{
  pref.begin("My-Prof", false);
  String device_id_str = pref.getString("device_id");

  char device_id[32];
  if (device_id_str.length() == deviceIdLen)
  {
    strcpy(device_id, device_id_str.c_str());
    device_id[deviceIdLen] = '\0';
    if (debugMode)
      Serial.println("device_id:" + String(device_id));
  }
  else
  {
    strcpy(device_id, GenerateID(deviceIdLen).c_str());
    device_id[deviceIdLen] = '\0';
    pref.putString("device_id", String(device_id));
    if (debugMode)
      Serial.println("Generate device_id:" + String(device_id));
  }
  pref.end();

  RacerBLE.deviceId = device_id;
  RacerBLE.firmwareVersion = FIRMWARE_VER;
  RacerBLE.hardwareVersion = HARDWARE_VER;
  RacerBLE.manufacturerName = "PLEN Project";

  RacerBLE.setup(ADVERTISING_UUID, SERVICE_UUID);
  RacerBLE.addDeviceInformationService();
  GET_BATTERY_VOLTAGE_CHARA = RacerBLE.addCharacteristic(GET_BATTERY_VOLTAGE, BLECharacteristic::PROPERTY_READ);
  SET_MOTOR_PWM_CHARA = RacerBLE.addCharacteristic(SET_MOTOR_PWM, BLECharacteristic::PROPERTY_WRITE_NR);
  SET_PORT_OUT_CHARA = RacerBLE.addCharacteristic(SET_PORT_OUT, BLECharacteristic::PROPERTY_WRITE_NR);
  SET_SERVO_POSITION_CHARA = RacerBLE.addCharacteristic(SET_SERVO_POSITION, BLECharacteristic::PROPERTY_WRITE_NR);
  BURST_COMMAND_CHARA = RacerBLE.addCharacteristic(BURST_COMMAND, BLECharacteristic::PROPERTY_WRITE_NR);
  GET_FUNCTIONS_CHARA = RacerBLE.addCharacteristic(GET_FUNCTIONS, BLECharacteristic::PROPERTY_READ);
  RacerBLE.startAdvertising();

  uint8_t byte0 = MOTOR_CH;
  uint8_t byte1 = (PORT_CH << 4) | SERVO_CH;
  uint16_t value = (byte1 << 8) | byte0;
  bleSetUint16Value(GET_FUNCTIONS_CHARA, value);

  RacerBLE.setCallback(SET_MOTOR_PWM_CHARA, onMotorPWMReceived, debugMode);
  RacerBLE.setCallback(SET_PORT_OUT_CHARA, onPortOUTReceived, debugMode);
  RacerBLE.setCallback(SET_SERVO_POSITION_CHARA, onServoPWMReceived, debugMode);
  RacerBLE.setCallback(BURST_COMMAND_CHARA, onBurstCommandReceived, debugMode);
}

void setMotorPWM(unsigned char motorPower) {
  const int neutral = 127;

  if (motorPower == neutral) {
    // 停止（両ブレーキ）
    ledcWrite(CHANNEL_MOTOR_A_PIN, 0);
    ledcWrite(CHANNEL_MOTOR_B_PIN, 0);
    return;
  }

  int power = motorPower - neutral;

  if (motorInv) {
    power *= -1;
  }

  uint8_t duty = abs(power);
  if(duty>127){
    duty = 127;
  }

  if (power > 0) {
    // 正転
    ledcWrite(CHANNEL_MOTOR_A_PIN, duty);
    ledcWrite(CHANNEL_MOTOR_B_PIN, 0);
  } else {
    // 逆転
    ledcWrite(CHANNEL_MOTOR_A_PIN, 0);
    ledcWrite(CHANNEL_MOTOR_B_PIN, duty);
  }
}

void setPortOUT(unsigned char port_out) {
  digitalWrite(PORT_0_PIN, (port_out & 0b0001) ? HIGH : LOW);  // bit 0 → PORT_0
  digitalWrite(PORT_1_PIN, (port_out & 0b0010) ? HIGH : LOW);  // bit 1 → PORT_1
}


void setServoPWM(unsigned char pwmValue) {
  if(servoInv){
    pwmValue = 255 - pwmValue;
  }
  ledcWrite(CHANNEL_SERVO_PIN, map(pwmValue, 0, 255, SERVO_TIME_MIN, SERVO_TIME_MAX));
}

void onMotorPWMReceived(const std::string& value) {
    if (value.length() < 1) return;

    uint8_t motor_power = static_cast<uint8_t>(value[1]);
    setMotorPWM(motor_power);
}

void onPortOUTReceived(const std::string& value) {
    if (value.length() < 1) return;

    uint8_t port_out = static_cast<uint8_t>(value[0]);
    setPortOUT(port_out);
}

void onServoPWMReceived(const std::string& value) {
    if (value.length() < 1) return;

    uint8_t servo_angle = static_cast<uint8_t>(value[1]);
    setServoPWM(servo_angle);
}

std::string lastBurstCommand = "";
void onBurstCommandReceived(const std::string& value) {
  if (value.length() < 7) return;
  if (value==lastBurstCommand) return;
  setMotorPWM(value[1]);
  setPortOUT(value[2]);
  setServoPWM(value[3]);
  lastBurstCommand = value;
}

void HardwareReset(){
  //　モータ停止
  setMotorPWM(127);
  // サーボ脱力
  ledcWrite(CHANNEL_SERVO_PIN, 0);
  // LED消灯
  setPortOUT(0);
  lastBurstCommand = "";
}

void onConnect()
{
}

void onDisconnect()
{
  HardwareReset();

  //　再接続
  RacerBLE.startAdvertising();
}

int AccelConvert(float accel)
{
  return (int)(accel * 100);
}

int AngleConvert(float angle)
{
  return (int)(angle * 100);
}

void LEDBlink(int msec, int cycle = 1000, double duty = 0.5, int max = 255, int min = 0)
{
  if ((double)(msec % cycle) / (double)cycle < duty)
  {
    ledcWrite(CHANNEL_STATUS_LED_PIN, max);
  }
  else
  {
    ledcWrite(CHANNEL_STATUS_LED_PIN, min);
  }
}

void BLEupdate()
{
  if (deviceConnectedFlag != RacerBLE.isConnected())
  {
    deviceConnectedFlag = RacerBLE.isConnected();
    if (deviceConnectedFlag)
    {
      onConnect();
    }
    else
    {
      onDisconnect();
    }
  }
  
  if (deviceConnectedFlag)
  {
    ledBlinkTime = 0;
    LEDBlink(millis() - ledBlinkTime, 250, 0.5, 255, 0);
  }
  else
  {
    if (ledBlinkTime == 0)
      ledBlinkTime = millis();
    LEDBlink(millis() - ledBlinkTime, 1000, 0.5, 255, 0);
  }
}

void setup()
{
  Serial.begin(115200);
  while (!Serial)
    delay(10); // wait for serial port to open!

  Serial.println("ESPRacer 2025");
  Serial.println("Copyright 2025 PLEN Project");

  SetupRacer();
  SetupBLE();
}

void PowerManagement()
{
  uint16_t batteryMv = (uint16_t)(analogReadMilliVolts(BATT_VOL_PIN) * 3.0);
  bleSetUint16Value(GET_BATTERY_VOLTAGE_CHARA, batteryMv);
}

void loop()
{
  PowerManagement();
  BLEupdate();

  while (millis() - lastSendTime < sendFreqency)
  {
    delay(1);
  }

  lastSendTime = millis();
}

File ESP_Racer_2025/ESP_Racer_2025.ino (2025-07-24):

// update: 2025/04/30  v3 コア完全対応 + タイマー再設計 + 広告名明示

#include <BLEDevice.h>
#include <BLEUtils.h>
#include <BLEServer.h>
#include <BLE2902.h>

/*========== BLE UUID ==========*/
#define SERVICE_UUID        "389CAAF0-843F-4D3B-959D-C954CCE14655"
#define GET_BATTERY_VOLTAGE "389CAAF1-843F-4D3B-959D-C954CCE14655"
#define SET_MOTOR_PWM       "389CAAF2-843F-4D3B-959D-C954CCE14655"
#define SET_PORT_OUT        "389CAAF3-843F-4D3B-959D-C954CCE14655"  
#define SET_SERVO_POSITION  "389CAAF4-843F-4D3B-959D-C954CCE14655"
#define BURST_COMMAND       "389CAAF5-843F-4D3B-959D-C954CCE14655"
#define GET_FUNCTIONS       "389CAAFF-843F-4D3B-959D-C954CCE14655"

/*========== I/O (Seeed Xiao ESP32-S3) ==========*/
#define power_led  10
#define servo_pin  6
#define motor0_pin 1
#define motor1_pin 3
#define port0_led  4
#define port1_led  5

/*========== globals ==========*/
BLECharacteristic *pCharacteristic1;
BLECharacteristic *pCharacteristic2;
BLECharacteristic *pCharacteristic3;
BLECharacteristic *pCharacteristic4;
BLECharacteristic *pCharacteristic5;
BLECharacteristic *pCharacteristic6;
BLEAdvertising   *pAdvertising;

unsigned char motor_power = 127;
unsigned char servo_power = 127;

volatile uint32_t interruptCounter = 0;     // 割り込みカウンタ
hw_timer_t *timer = nullptr;
portMUX_TYPE timerMux = portMUX_INITIALIZER_UNLOCKED;
static int light = LOW;                     // LED トグル用

/*========== timer ISR ==========*/
void IRAM_ATTR onTimer() {
  portENTER_CRITICAL_ISR(&timerMux);
  ++interruptCounter;
  portEXIT_CRITICAL_ISR(&timerMux);
}

/*========== BLE Callbacks ==========*/
class MyCallbacks : public BLECharacteristicCallbacks {
  void onWrite(BLECharacteristic *pCharacteristic) override {
    String value = pCharacteristic->getValue();
    if (value.length() < 4) return;         // データ不足時は無視

    motor_power = value[1];                 // DC モータ
    if (value[2] == 3) {                    // ポート LED
      digitalWrite(port0_led, HIGH);
      digitalWrite(port1_led, HIGH);
    } else {
      digitalWrite(port0_led, LOW);
      digitalWrite(port1_led, LOW);
    }
    servo_power = value[3];                 // サーボ
  }
};

class ServerCallbacks : public BLEServerCallbacks {
  void onConnect(BLEServer*) override {
    Serial.println("connect.");
    motor_power = servo_power = 127;
    timerAlarm(timer, 100'000, true, 0);    // LED：0.1 s 周期
  }
  void onDisconnect(BLEServer*) override {
    Serial.println("disconnect.");
    motor_power = servo_power = 127;
    timerAlarm(timer, 500'000, true, 0);    // LED：0.5 s 周期
  }
};

/*========== SETUP ==========*/
void setup() {
  Serial.begin(115200);
  Serial.print("starting...");

  pinMode(servo_pin,  OUTPUT);
  pinMode(motor0_pin, OUTPUT);
  pinMode(motor1_pin, OUTPUT);
  pinMode(power_led,  OUTPUT);
  pinMode(port0_led,  OUTPUT);
  pinMode(port1_led,  OUTPUT);

  /*----- ハードウェアタイマー -----*/
  timer = timerBegin(1'000'000);               // 1 MHz (1 µs 分解能)
  timerAttachInterrupt(timer, &onTimer);
  timerAlarm(timer, 500'000, true, 0);          // 初期：0.5 s 周期

  /*----- BLE 初期化 -----*/
  BLEDevice::init("ESP Racer");
  BLEServer  *pServer  = BLEDevice::createServer();
  BLEService *pService = pServer->createService(SERVICE_UUID);

  pCharacteristic1 = pService->createCharacteristic(GET_BATTERY_VOLTAGE, BLECharacteristic::PROPERTY_READ);
  pCharacteristic2 = pService->createCharacteristic(SET_MOTOR_PWM,       BLECharacteristic::PROPERTY_WRITE_NR);
  pCharacteristic3 = pService->createCharacteristic(SET_PORT_OUT,        BLECharacteristic::PROPERTY_WRITE_NR);
  pCharacteristic4 = pService->createCharacteristic(SET_SERVO_POSITION,  BLECharacteristic::PROPERTY_WRITE_NR);
  pCharacteristic5 = pService->createCharacteristic(BURST_COMMAND,       BLECharacteristic::PROPERTY_WRITE_NR);
  pCharacteristic6 = pService->createCharacteristic(GET_FUNCTIONS,       BLECharacteristic::PROPERTY_READ);

  pCharacteristic5->setCallbacks(new MyCallbacks());
  pServer->setCallbacks(new ServerCallbacks());

  pService->start();

  /*----- 広告データに名前を明示 -----*/
  pAdvertising = pServer->getAdvertising();
  pAdvertising->addServiceUUID(SERVICE_UUID);
  pAdvertising->setScanResponse(true);          // 名前はスキャン応答へ
  BLEAdvertisementData scanData;
  scanData.setName("ESP Racer");                // ブラウザ等に表示される名前
  pAdvertising->setScanResponseData(scanData);
  pAdvertising->start();

  Serial.println("done.");
}

/*========== LOOP ==========*/
void loop() {
  constexpr unsigned int control_phase = 16'000;                 // 16 ms
  unsigned int servo_on = 1'500 + (servo_power - 127) * 4;       // 1012–1992 µs
  unsigned int motor_on = control_phase * abs(motor_power - 127) / 200;

  /*----- 電源 LED 点滅 -----*/
  if (interruptCounter > 0) {
    portENTER_CRITICAL(&timerMux);
    --interruptCounter;
    portEXIT_CRITICAL(&timerMux);

    light ^= 1;
    digitalWrite(power_led, light);
  }

  /*----- DC モータ & サーボ制御 -----*/
  if (motor_on > servo_on) {                 // モータ優先
    if (motor_power > 127) {                 // 正転
      digitalWrite(motor0_pin, HIGH);
      digitalWrite(motor1_pin, LOW);
      motor_on += control_phase / 4;
    } else if (motor_power < 127) {          // 逆転
      digitalWrite(motor0_pin, LOW);
      digitalWrite(motor1_pin, HIGH);
      motor_on += control_phase / 4;
    } else {                                 // 停止
      digitalWrite(motor0_pin, HIGH);
      digitalWrite(motor1_pin, HIGH);
    }
    digitalWrite(servo_pin, HIGH);
    delayMicroseconds(servo_on);
    digitalWrite(servo_pin, LOW);
    delayMicroseconds(motor_on - servo_on);
    digitalWrite(motor0_pin, LOW);
    digitalWrite(motor1_pin, LOW);
    delayMicroseconds(control_phase - motor_on);

  } else {                                   // サーボのみ
    digitalWrite(servo_pin, HIGH);
    delayMicroseconds(servo_on);
    digitalWrite(servo_pin, LOW);
    delayMicroseconds(control_phase - servo_on);
  }
}

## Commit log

2021-05-26 プロジェクトの移動
2021-05-26 タイトルロゴ
2021-05-26 ロゴサイズの修正
2021-05-26 背景色の変更
2021-05-26 デザインの修正
2021-05-26 画像の修正
2021-05-26 色の修正
2021-05-27 スタートボタンの修正
2021-06-02 アイコンの修正
2021-06-02 名称の修正
2021-06-02 表示の修正
2021-06-02 ボタンの修正
2021-06-02 説明書の更新
2021-06-02 説明書の修正
2021-06-03 ローディング画面の修正
2021-06-09 設定の修正
2021-06-18 誤字修正
2025-06-25 Add files via upload
    2025年度版ESP Racer（ESP32S3対応）ソースコード
2025-07-01 add pcb design
    [DRV8835DSST.step, ESP_Racer_2025.kicad_pcb, ESP_Racer_2025.kicad_sch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]
2025-07-01 update pcb
2025-07-02 pcb fix
    [53047-0210.step, 53047-0310.step, ESP_Racer_2025.kicad_pcb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]
2025-07-02 fix pcb
    [ESP_Racer_2025.kicad_pcb]
2025-07-17 add PIO
    [ESP_Racer_2025.kicad_sch]
2025-07-28 update firmware
    [ESP_Racer_2025.kicad_sch]
2025-07-30 change LED blink
2025-07-30 fix hardware errors
    [ESP_Racer_2025.kicad_sch]
2025-08-13 Restore LED pin
2025-08-14 pcb update
    [ESP_Racer_2025.kicad_pcb, ESP_Racer_2025.kicad_sch, bom.csv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]
